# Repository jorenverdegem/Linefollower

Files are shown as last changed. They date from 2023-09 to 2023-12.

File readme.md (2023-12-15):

# LineFollower PLAN B:

400920108_895944135587999_7262908235151916565_n

# LineFollower PLAN A:

398428672_725404612801147_6601868790741897883_n

## specifications (Plan A)

microcontroller: ATmega32u4

motors: Mini Micro Metal Gear Motor 6V DC - Ratio 30:1

h-bridge: DRV8833 Dual Motor Driver Carrier

sensors: QTR-8A Reflectance Sensor Array

batteries: 18650 Li-ion batterijen

wireless communication: HC-05 Bluetooth module

distance sensor - motors: 70 mm

weight: 182 g

speed: 0.612 m/s

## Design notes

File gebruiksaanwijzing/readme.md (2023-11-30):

# Gebruiksaanwijzing

### opladen / vervangen batterijen
De batterijen kunnen van de wagen worden gehaald door de rekker rond de arduino los te maken. Indien de batterijen te stevig vast zitten kan men steeds een schroevendraaier gebruiken om ze los te krijgen.
Het is aangeraden steeds de spanning van deze batterijen te controleren met een multimeter. Als deze geen 8V meer leveren laad je ze best op. Dit kan door ze in liitokala oplader te steken, die is te vinden in de BOM.
Vanaf de lampjes groen zijn, hebben de batterijen weer voldoende spanning en kan de wagen zonder problemen even door rijden.

### draadloze communicatie
#### verbinding maken
Om verbinding te maken met de smartphone zorg je eerst dat de wagen voorzien is van de correcte spanning (de twee batterijen hebben samen >8V). 
Als tweede neem je de smarthpone en download je de app "Serial Bluetooth Terminal" (android). Deze app zal het mogelijk te communiceren met onze wagen.
Dit gebeurt aan de hand van verschillende commando's. De meest gebruikte commando's kunnen eenvoudig in 4 drukknoppen worden verwerkt. 
Deze 4 knoppen zijn op de foto in het geel aangeduid. Om deze net zoals mij te programmeren druk je lang op de knop en stel je de volgende zaken in:
Knop 1 -> Name: "on", Value: "run on"
Knop 2 -> Name: "off", Value: "run off"
Knop 3 -> Name: "debug", Value: "debug"
Knop 4 -> Name: "?", "cmd"

bewerkt403773356_2250373231799713_3687328011572819282_n

Om de connectie te maken ga je eerst naar de bluetoothinstelling van de telefoon en zoek je "HC-05". Vervolgens maak je verbinding en gebruik je de code "1234".
Eenmaal verbonden, kan je naar de app gaan en zou je deze bij "devices" moeten zien staan. Als laatste druk je op "connect" (de gele cirkel op bovenstaande foto). 
Als je de boodschap "connected" te zien krijgt, ben je volledig verbonden en klaar om commando's uit te sturen.

#### commando's
Er zijn verschillende commando's die gebruikt kunnen worden om parameters van de robot in te stellen, maar ook om zaken uit te lezen. De eerste 4 commando's zijn reeds verwerkt in de 4 drukknoppen en doen het volgende:
"on" -> stuurt commando "run on" -> Dit zal de motoren starten en de wagen doen rijden.
"off" -> stuurt commando "run off" -> Dit zal de motoren en de wagen doen stoppen.
"debug" -> stuurt commando "debug" -> Je krijgt een oplijsting van alle ingestelde parameters waarmee de wagen momenteel rijdt. 
"?" -> stuurt commando "cmd" -> Je krijgt een oplijsting van alle mogelijke commando's die buiten de knoppen ook kunnen worden ingegeven (zie foto).
405417769_639606544789889_332189492948155658_n

Volgende commando's kunnen dus ook nog worden ingegeven, en stellen een bepaalde parameter in:
set cycle [µs]  
set power [0..255]  
set diff [0..1]  
set kp [0..]  
set ki [0..]  
set kd [0..]

# vb. set ki 0.7 

Als laatste zijn er nog 2 andere commando's om de sensoren te calibreren. Dit wordt hieronder verder verduidelijkt.
calibrate black  
calibrate white  

### kalibratie
Wanneer er voor de eerste keer wordt gereden op een bepaald parkour is het belangrijk om de sensoren te calibreren. Dit zal er voor zorgen dat er een duidelijk verschil tussen wit en zwart wordt herkent.

# stap 1:
Plaats de wagen op een volledig wit stuk, en voer het commando "calibrate white" in. Wacht even tot je "done" ziet verschijnen.
# stap 2:
Plaats de wagen op een volledig zwart stuk, en voer het commando "calibrate black" in. Wacht even tot je "done" ziet verschijnen.

-> Nu zouden de sensoren een duidelijk verschil moeten uitlezen. Dit kan je controleren door "debug" in te voeren, en de "black" en "white" waardes te controleren. Deze moeten ver genoeg uit elkaar liggen om correct te kunnen werken.

### settings
De robot rijdt stabiel met volgende parameters:
405311322_893484695519741_7041870474847189614_n

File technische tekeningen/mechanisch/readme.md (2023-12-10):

Op deze pagina vind je het volgende terug:

- Mechanische tekening van de PCB.
- Mechanische tekening van de spoiler, die met de 3D printer kan worden afgeprint.

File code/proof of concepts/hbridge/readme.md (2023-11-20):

# H-Bridge proof of concept

Minimale hard- & software die aantoont dat 2 motoren onafhankelijk van elkaar kunnen draaien, en (traploos) regelbaar zijn in snelheid en draairichting.
Hiervoor wordt gebruik gemaakt van 2 "Mini Micro Metal Gear Motor 6V DC - Ratio 30:1" motoren en als H-brug gebruiken we de "DRV8833 Dual Motor Driver Carrier".

## Functionaliteit:

Het geschreven programma zal in een loop demonstreren hoe de motoren geleidelijk aan versnellen tot het maximale snelheid, en vervolgens weer vertragen naar 0. 
Vervolgens wordt gedemonstreerd dat ze ook in tegengestelde richting kunnen draaien, en ook afzonderlijk van elkaar een andere draairichting kunnen aannemen.

## Arduinocode:

image (11)
image (12)
image (13)

In de setup worden de pinnen die verbonden zijn met de H-brug als OUTPUT geconfigureerd en worden de motoren uitgezet.
Vervolgens begint te "void loop" functie waarin verschillende zaken gebeuren:
  1. De motoren gaan van stilstand geleidelijk aan naar hun maximale snelheid.
  2. De motoren blijven 2 seconden aan hun maximale snelheid draaien.
  3. De motoren vertragen van hun maximale snelheid naar stilstand.
  4. De motoren blijven 2 seconden uit.
  5. De maximale snelheid in tegengestelde draairichting worden op beide motoren gedemonstreerd voor 2 seconden.
  6. De motoren blijven 2 seconden uit.
  7. De motoren draaien 2 seconden aan hun maximale snelheid, maar beide met een andere draairichting.
  8. De motoren blijven 1 seconde uit.
  9. de motoren draaien 2 seconden aan hun maximale snelhied, maar nu beide in de andere richting dan de vorige stap.
  10. De motoren blijven 1 seconde uit

Vervolgens zijn nog 3 andere functies in gemaakt. Deze zullen ervoor zorgen dat we via de "spin_and_wait" functie overzichtelijk de snelheid kunnen geven aan de 2 motoren.
Ook wordt hier duidelijk gemaakt dat de draairichting moet veranderen als we een negatieve waarde ingeven en wordt de snelheid geschreven naar de seriële monitor.

## Elektronisch schema:

Het elektronisch schema voor deze schakeling ziet er als volgt uit:
Schema H-bruggen

## Testresultaten:

Op de seriële monitor kunnen we mooi volgen welke snelheid de motoren op dit moment hebben aangenomen:
image (14)

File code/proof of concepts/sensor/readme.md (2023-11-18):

# Sensoren proof of concept

minimale hard- en software die aantoont dat minimaal 6 sensoren onafhankelijk van elkaar kunnen uitgelezen worden (geen calibratie, normalisatie of interpolatie). Hierbij moet een zo groot mogelijk bereik van de AD converter benut worden (indien van toepassing).
Hiervoor wordt de QTR-8A gebruikt, waarbij de laatste 2 sensoren van de printplaat worden afgebroken.

## Arduino code:

De arduino code ziet er als volgt uit:

image (9)

Hierbij maken we gebruik van de QTRSensors.h library. Deze maakt het mogelijk om de sensor evenvoudig te configureren en de waardes uit te lezen.
Vervolgens worden deze 6 sensorwaardes naast elkaar geprint op de seriële monitor. Het resultaat ziet er als volgt uit:

image (10)

## Elektronisch schema:

Een elektronisch schema is bij deze schakeling overbodig, aangezien de 6 analoge outputs van de sensoren gewoon moeten verbonden worden met de 6 analoge inputs van de arduino.
Verder moet de sensor enkel nog gevoed worden met 5V, en moet ook de gnd worden verbonden.

QTR

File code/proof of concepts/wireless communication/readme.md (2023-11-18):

# draadloze communicatie proof of concept
Minimale hard- en software waarmee aangetoond wordt dat duplex kan gecommuniceerd worden tussen de microcontroller en een smartphone, gebruik makend van de HC-05 Bluetoothmodule.
Om de werking van de bluetoothmodule te demonstreren is een code geschreven waarbij we in 2 richtingen communiceren.

## Functionaliteit:
Als eerste zal de microcontroller een drukknop uitlezen en doorsturen naar de smartphone vanaf deze wordt ingedrukt.
Anderzijds kan de toestand van de "built-in led" op de microcontroller gewijzigd worden door 2 knoppen op de smartphone.
Als laatste is het ook mogelijk om tekstberichten van de smartphone naar de pc te sturen, en omgekeerd.

## Arduino code:
De arduino code ziet er als volgt uit:


Als eerste valt op dat we gebruik maken van de library "SoftwareSerial.h". Deze zorgt ervoor dat we een tweede softwarematige seriële monitor kunnen aanmaken, die wordt gebruikt door de smarthphone.
Als we kijken naar de eerste "if" structuur in de "void loop()" functie zien we dat de data wordt ingelezen van de seriële monitor van de smartphone, en wordt geschreven naar de seriële monitor van de computer.
Het omgekeerde gebeurd in de tweede "if" structuur. Op deze manier kunnen we al in twee richtingen berichten zenden.

In de derde "if" structuur wordt gezocht naar een '0' of een '1' in de data die binnenkomt vanaf de gsm. Dit is wat de knop op de gsm zal doorsturen als we de LED op de microcontroller willen laten branden.

Als laatste is ook een interruptfunctie toegevoegd met een debouncefunctie om de knop aan de microcontroller uit te lezen, en vervolgens een boodschap naar de gsm te sturen.
Dit principe kwam al eerder terug in de "Proof of concepts: interrupt".

## Elektronisch schema
Het elektronisch schema voor deze schakeling ziet er als volgt uit:

Merk op dat de RX van de bluetoothmodule niet rechtsreeks verbonden is met de TX van de microcontroller! Dit is belangrijk aangezien de HC-05 Bluetoothmodule met 3.3V signalen verwacht.
De arduino stuurt signalen van 5V. Daarom maken we een spanningsdeler met behulp van 2 weerstanden zodat we de 5V een stuk kunnen reduceren.

## Testresultaten
Op de smartphone ziet de seriële monitor er als volgt uit:
370057969_310741495226934_2358127417559545938_n
Onderaan zijn de knoppen "on" en "off" te zien. Deze werden ingedrukt en verstuurden een '1' en een '0'. De LED aan de microcontroller ging effectief aan en uit wanneer op de corresponderende knoppen werd gedrukt.
Vervolgens is op de knop aan de microcontroller gedrukt. Hier ontvingen we correct het bericht "De knop is ingedrukt!". Als laatste is via de seriële monitor van de computer nog een testbericht gestuurd naar de gsm.
Hierop is het antwoord "test van gsm naar pc" verstuurd. Dit zien we dan ook verschijnen op seriële monitor van de computer:


Als laatste is ook op de foto te zien dat de baudrate van onze seriële monitor is ingesteld op 9600 baud. Dit is belangrijk aangezien we dezelfde keuze hebben gemaakt in de arduinocode. Deze moeten overeenkomen!

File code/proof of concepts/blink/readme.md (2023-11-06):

# blink proof of concept
Om een led simpelweg te doen knipperen via een arduino, is de volgende code geschreven:



De built-in led in de arduino wordt geconfigureerd als output. Deze output wordt vervolgens herhaaldelijk om de seconde hoog gezet.
Wanneer we in de toekomst willen testen of de microcontroller nog steeds werkt naar behoren, kan dit programma simpelweg worden upgeload om zeker te zijn van ons zaak.

(Een schema wordt verder niet weergegeven, aangezien we de interne led van de arduino doen knipperen. Er wordt verder niks geschakeld aan de arduino.)

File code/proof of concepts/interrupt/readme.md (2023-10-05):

# start/stop interrupt proof of concept
Om de werking van een start/stop interrupt te demonstreren op een arduino, waarin softwarematig gezorgd is voor een debounce van de schakelaar, is de volgende code geschreven:

image (1)

De code werkt als volgt: als de schakelaar wordt ingedrukt waarmee men een start of stop signaal wilt genereren, zal via de "attachInterrupt" functie de loop hardwarematig onderbroken worden. Er hoeft dus niet telkens gepolled worden in de software om te kijken of de knop al dan niet is ingedrukt.
Als de intterupt wordt getriggerd wordt de functie "void interrupt()" uitgevoerd. Hierin wordt ter demonstratie de toestand van een led gewijzigd. Dit kan uiteraard vervangen worden door een start/stop signaal.

In deze interrupt zorgt de "millis()" functie er verder voor dat er geen debouncing kan optreden bij het indrukken van de schakelaar. De interrupt moet 100 ms actief zijn alvorens de functie effectief wordt uitgevoerd. Als ons knop dus even zou trillen, zal de functie geen meerdere keren worden uitgevoerd.

Vb: de knop trilt 3x met daartussen telkens 10 ms -> de functie zal maar 1x worden uitgevoerd aangezien de "if" functie zal zorgen voor een kleine delay.

Het elektronisch schema voor deze schakeling ziet er als volgt uit:



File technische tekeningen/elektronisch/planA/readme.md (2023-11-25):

## PCB ontwerp:



## PCB Top view:



## PCB Bottom view:



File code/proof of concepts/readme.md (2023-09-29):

# Proof of Concepts

Een proof of concept is een combinatie van minimale hard- en software om eenvoudig aan te tonen dat iets werkt.  
Proof of concepts kunnen enerzijds als eerste poging dienen om een bepaald onderdeel van het project werkend te krijgen. Anderzijds kunnen ze tijdens het debuggen van het finale project dienen als test om eventuele hardware problemen te elimineren bij onduidelijke problemen.
<br />  
<br />
Een proof of concept bestaat uit
* een elektronisch schema (indien van toepassing)
* minimale code om de voorop gestelde zaken te demonstreren
* minimale uitleg / aandachtspunten
<br />
De elektronische schakelingen van de proof of concepts komen bij voorkeur overeen met deze van de uiteindelijke linefollower, zodat de code zonder aanpassingen op het finale project kan draaien.

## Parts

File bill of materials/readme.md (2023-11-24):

## bill of materials
<br />

|volgnummer |naam |omschrijving |nieuw/recup |kostprijs/stuk |aantal  |subtotaal |
|--- |---- |--- |--- |--- |---  |--- |
|1 |Microcontroller |ATmega32u4 (Arduino Leonardo) |Recup |€12,99 |1 |€12,99 |
|2 |Mini Micro Metal Gear Motor 30:1 |6V DC Gear Motor |Nieuw |€3,56 |2 |€7,12 |
|3 |H-brug |DRV8833 Dual Motor Driver Carrier |Nieuw |€12,52 |1 |€12,52 |
|4 |Infrared Reflection Sensors (8) |QTR-8A Reflectance Sensor Array |Nieuw |€16,13 |1 |€16,13 |
|5 |18650 Li-ion Batterijen |Rechargeable Battery (3,7V - 19800mAh)|Nieuw |€2,63 |2 |€5,26 |
|6 |Batterijhouder |18650 Dubbele batterijhouder |Nieuw |€2,39 |1 |€2,39 |
|7 |Batterijoplader |LiitoKala Lii-L2 3,7V 18650 |Nieuw |€10,17 |1 |€10,17 |
|8 |Bluetooth Module |HC-05 |Recup |€11,96 |1 |€11,96 |
|9 |Wielhouders |Micro Metal Gearmotor Bracket Pair |Nieuw |€5,39 |1 |€5,39 |
|10 |Wielen |Polulu wheel 40x7mm Pair - Red |Nieuw |€7,69 |1 |€7,69 |
|11 |Weerstanden |1x1kOhm en 1x2kOhm OF 3x1kOhm |Recup |/ |3 |/ |
|12 |Dupont-draadjes |20xman-vrouw en 5xman-man |Recup |/ |25 |/ |

### Totale kostprijs: €91,62

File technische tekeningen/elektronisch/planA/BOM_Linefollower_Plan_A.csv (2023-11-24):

ID | Name | Designator | Footprint | Quantity | Manufacturer Part | Manufacturer | Supplier | Supplier Part | Price
1 | 18650x2 | H1 | H18650 | 1
2 | ARDUINO_LEONARDO | U1 | ARDUINO_LEONARDO | 1
3 | DRV8833 | U2 | DRV8833 DUAL MOTOR DRIVER CARRIER | 1
4 | HC05 | U3 | HC-05 | 1 | HC05
5 | QTR8A | U4 | QTR8A | 1 | QTR8A | POLOLU | POLOLU
6 | Micro metal gearmotor | U5,U6 | MICRO METAL GEAR MOTOR | 2 | 3062 | Pololu | Pololu | 3062

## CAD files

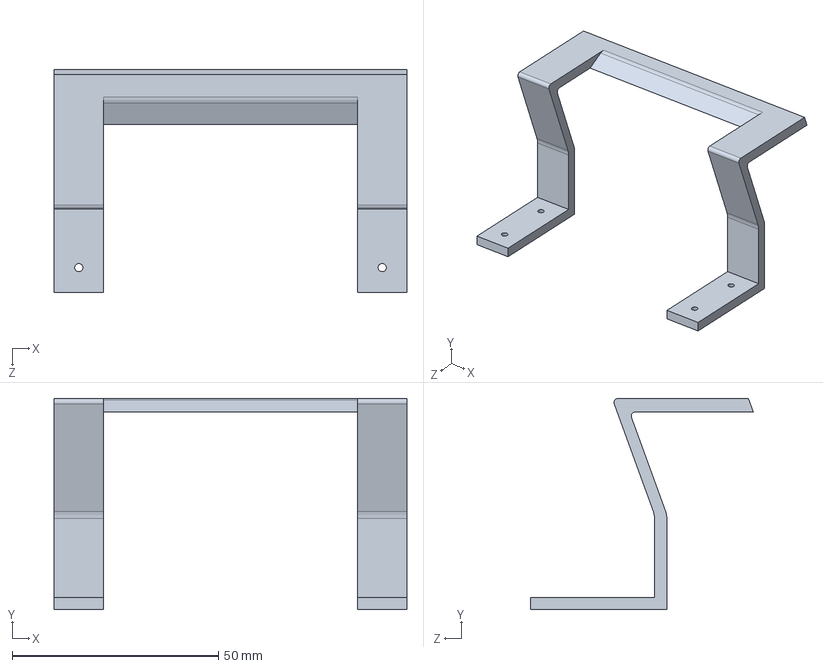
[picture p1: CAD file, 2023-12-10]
technische tekeningen/mechanisch/spoiler.SLDPRT
85.5 x 51.2 x 53.9 mm

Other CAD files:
technische tekeningen/mechanisch/Spoiler.STL

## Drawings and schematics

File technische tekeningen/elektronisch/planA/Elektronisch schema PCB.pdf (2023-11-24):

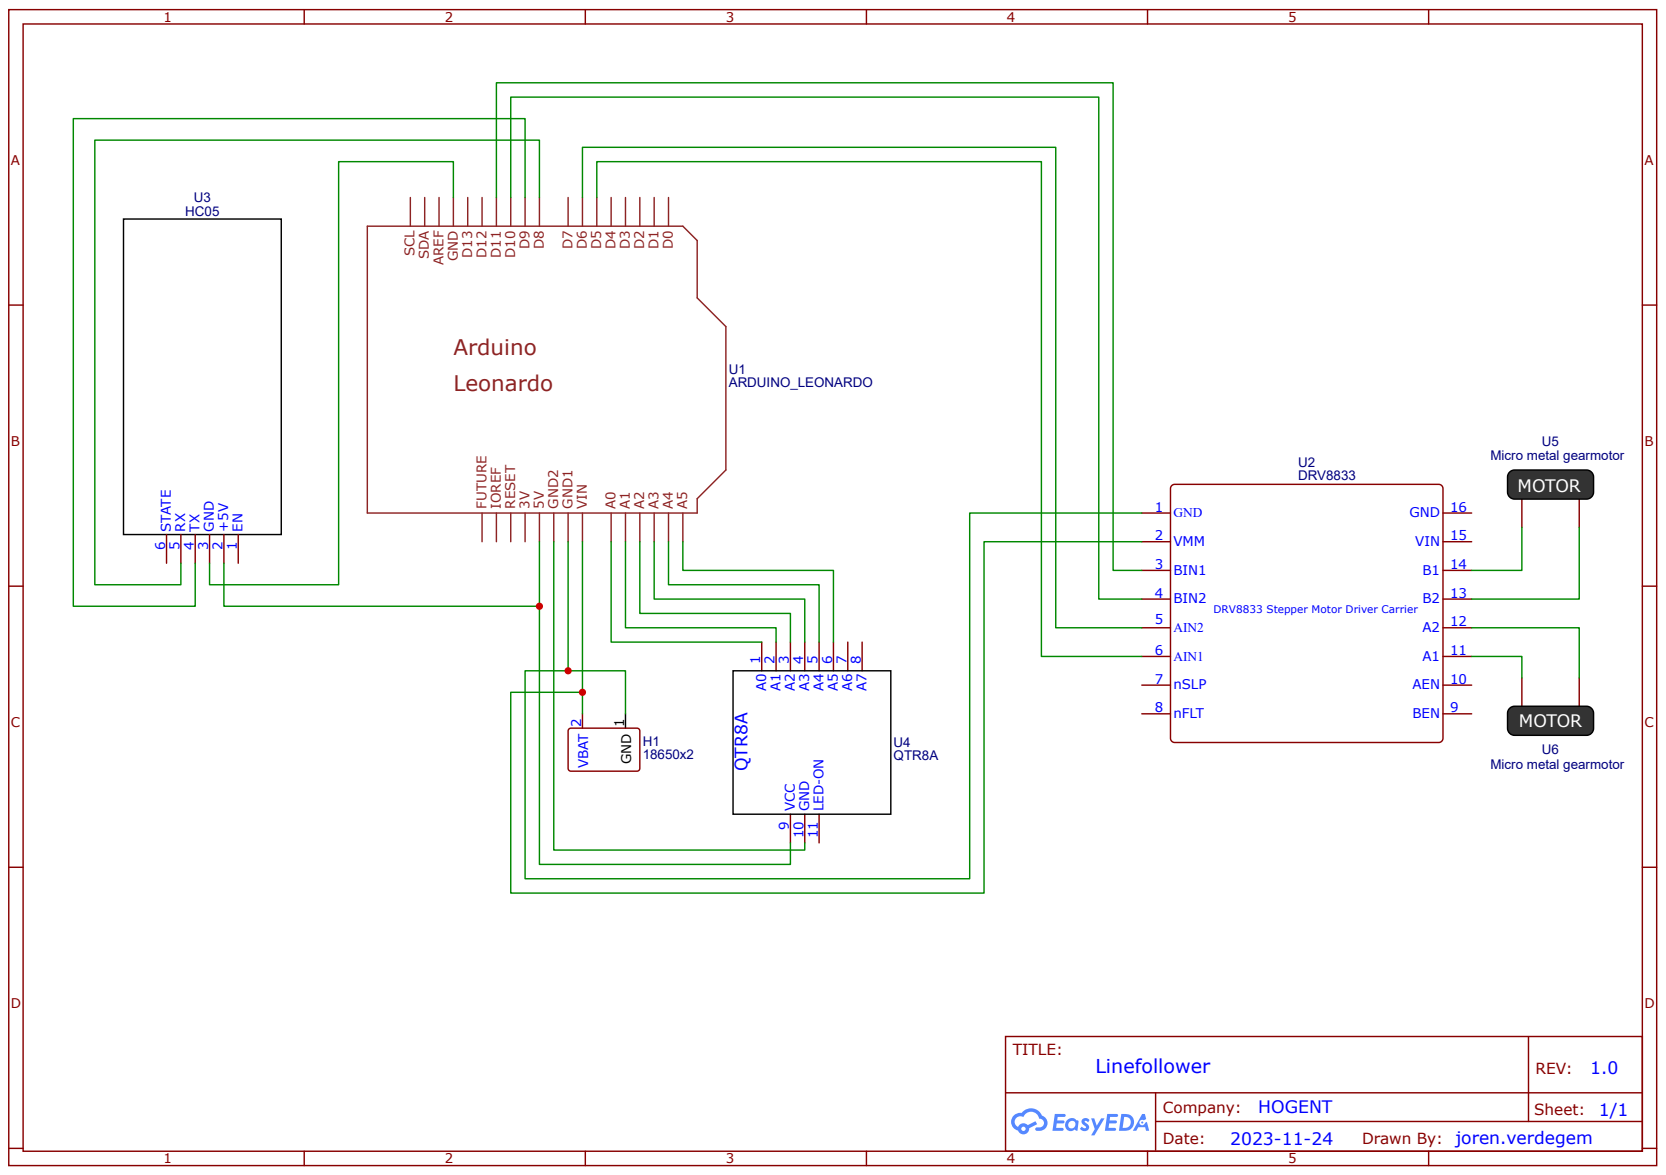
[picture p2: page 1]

DRV8833 Stepper Motor Driver Carrier

Drawn By: joren.verdegem

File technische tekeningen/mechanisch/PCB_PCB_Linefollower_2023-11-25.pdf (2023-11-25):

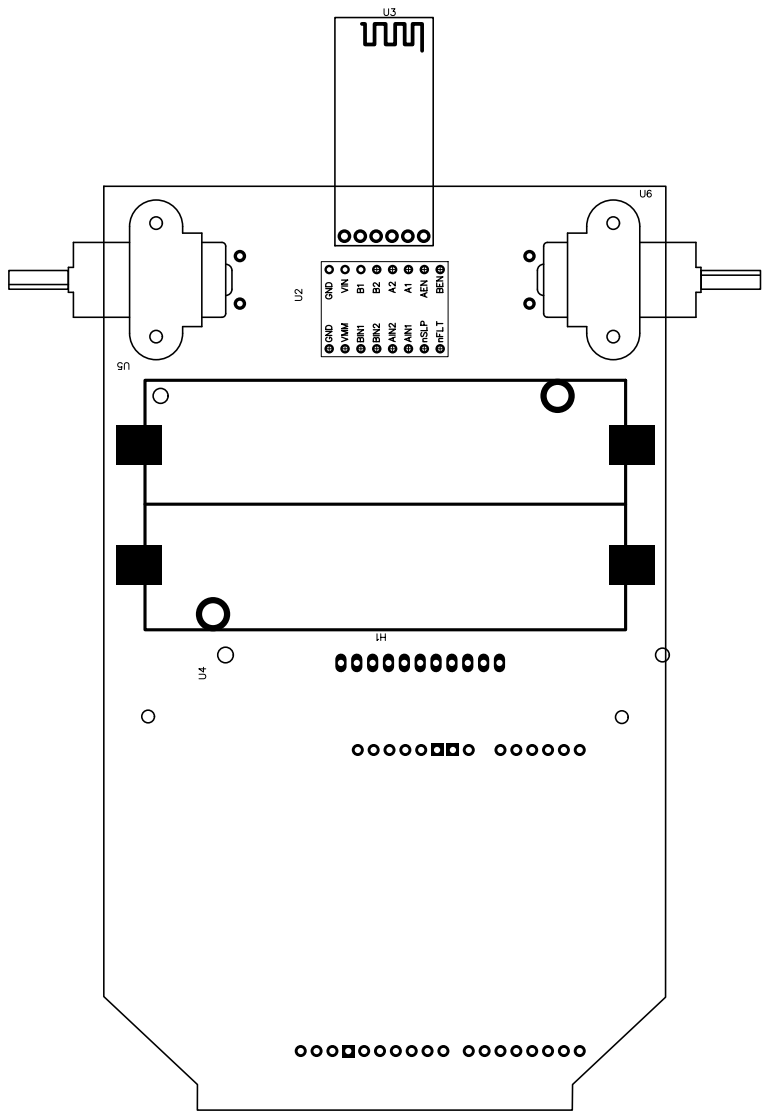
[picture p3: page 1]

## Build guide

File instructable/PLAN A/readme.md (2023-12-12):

# Instructable

Nadat we Plan B hebben samengesteld, kiezen we ervoor om het resultaat nog mooier afwerken. Het idee is om een printplaat te ontwerpen, die kan dienen als frame voor onze wagen. Hierbij zullen dus geen dupon meer nodig zijn, wat zal zorgen voor een mooier afgewerkt geheel. Op de printplaat zorgen we dus voor alle connecties tussen de verschillende componenten, met bijhorende gaten zodat we onze componenten hierop kunnen solderen.

### stap 1

<br />

|volgnummer |naam |omschrijving |nieuw/recup |kostprijs/stuk |aantal  |subtotaal |
|--- |---- |--- |--- |--- |---  |--- |
|1 |Microcontroller |ATmega32u4 (Arduino Leonardo) |Recup |€12,99 |1 |€12,99 |
|2 |Mini Micro Metal Gear Motor 30:1 |6V DC Gear Motor |Nieuw |€3,56 |2 |€7,12 |
|3 |H-brug |DRV8833 Dual Motor Driver Carrier |Nieuw |€12,52 |1 |€12,52 |
|4 |Infrared Reflection Sensors (8) |QTR-8A Reflectance Sensor Array |Nieuw |€16,13 |1 |€16,13 |
|5 |18650 Li-ion Batterijen |Rechargeable Battery (3,7V - 19800mAh)|Nieuw |€2,63 |2 |€5,26 |
|6 |Batterijhouder |18650 Dubbele batterijhouder |Nieuw |€2,39 |1 |€2,39 |
|7 |Batterijoplader |LiitoKala Lii-L2 3,7V 18650 |Nieuw |€10,17 |1 |€10,17 |
|8 |Bluetooth Module |HC-05 |Recup |€11,96 |1 |€11,96 |
|9 |Wielhouders |Micro Metal Gearmotor Bracket Pair |Nieuw |€5,39 |1 |€5,39 |
|10 |Wielen |Polulu wheel 40x7mm Pair - Red |Nieuw |€7,69 |1 |€7,69 |
|11 |Pinheaders | |Recup |/ |40 |/ |

Nu we alle componenten hebben, kunnen we de printplaat beginnen ontwerpen. Dit werd gedaan via de website: https://easyeda.com/editor .
Het ontwerpen van deze printplaat gebeurd in 3 stappen.

### stap 2

Je tekent een elektronisch schema, waarbij je alle componenten terugzoekt in het programma. Het is belangrijk dat je de exacte componenten invoegt, zodat de afmetingen in de latere fases overeenkomen met onze componenten. Het elektrisch schema dat ik heb ontworpen is terug te vinden via de volgende link: https://github.com/jorenverdegem/Linefollower/tree/main/technische%20tekeningen/elektronisch/planA . Hierbij kan de JSON worden gebruikt om rechtsreeks in het programma te voegen, dan hoef je het schema niet meer zelf te tekenen.

## !BELANGRIJK! 
De component "DRV8833" staat verkeerd getekend in dit programma. De gaatjes voor de pinnen zijn te klein, en de component is 5 mm te dik getekend. Je gaat hier dus best opzoek naar de juiste component, of past de tekening aan zodat ze overeen komt met de afmetingen uit de datasheet.
Let er verder ook op dat je de QTR-8A sensor niet perfect in het midden plaatst! Wij maken enkel gebruik van de eerste 6 sensoren (want een arduino heeft maar 6 analoge inputs), waardoor het midden van de sensor zich op een andere positie bevindt. Zorg dat dit overeenkomt!

### stap 3

Nadat je het elektronisch schema hebt gemaakt, en gecontroleerd hebt dat alles correct is aangesloten kan je beginnen aan het mechanisch ontwerp. Hierbij kies je waar welke component staat op de printplaat, en kan je ook de vorm aanpassen. Mijn mechanische tekening is terug te vinden via de volgende link: https://github.com/jorenverdegem/Linefollower/blob/main/technische%20tekeningen/elektronisch/planA/readme.md .

### stap 4

Als laatste ga je op de mechanische tekening de verbindingen tekenen. Je kan dit automatisch laten genereren, maar ik raad aan om handmatig de verbindingen te leggen. Zo controleer je zelf nog eens of alles goed zit aangesloten. Mijn uiteindelijke PCB ontwerp is te vinden via de volgende link: https://github.com/jorenverdegem/Linefollower/tree/main/technische%20tekeningen/elektronisch/planA .

### stap 5

Nu alles is getekend kan je de pcb bestellen en hem laten maken. Dit alles duurt tussen de 1 à 2 weken.

#### Resultaat:

403398636_370587428807641_8804265821271583842_n

386886413_1037275554153914_3952061519202620705_n

### stap 6

Als de printplaat is toegekomen kan je starten met het solderen van je componenten.
- Waar de arduino komt, soldeer je pinheaders. Op deze manier kan je de arduino er steeds opklikken en weer afhalen.
- De QTR-8A sensor soldeer je aan de onderkant van de printplaat, zodat de sensoren naar de grond kijken.
- De batterijhouder kan je vastkleven met stevige lijm tegen de printplaat. De 2 draadjes soldeer je vast op de voorziene metalen vierkantjes.
- De bluetoothmodule kan je rechtopstaand solderen. Zorg ervoor dat de pinnen (zoals vcc en gnd) overeenkomen met de juiste gaatjes op de pcb.
- De motoren maak je vast met de bijhorende beugels, de gaatjes zijn hiervoor perfect gepositioneerd.
- De H-brug soldeer je ook vast op de correcte plek

Als alles goed vast zit kan je het geheel opnieuw beginnen testen. Indien er iets misloopt is het interessant om de proof of concepts er weer bij te halen en alles terug afzonderlijk te testen.
Zo was bij mij het geval dat een van de motoren kapot was gegaan. Deze werd zeer warm en draaide niet meer bij zeer lage snelheden. Ook als de reductie ervan tussen werd gehaald deden dezelfde problemen zich voor.

Indien je net zoals mij de fout hebt gemaakt om de component "DRV8833" zonder aanpassen in het pcb programma te gebruiken, kan je de component toch nog solderen aan de hand van vrouwelijke pinheaders, die wat schuin worden geplaatst. Het resultaat oogt iets minder mooi, maar ziet er als volgt uit:

377144747_2392994354217988_3845947637720984982_n

### stap 7

Proficiat! Nu alles werkt heb je een werkend geheel! Nu de wagen tot leven is gekomen kan je gaan spelen met de verschillende parameters, tot je het snelheidsrecord breekt!
Om het geheel helemaal af te werken kan je er eventueel ook een spoiler op monteren. Een getekende spoiler die kan worden afgedrukt met een 3D printer is te vinden via de volgende link:
https://github.com/jorenverdegem/Linefollower/tree/main/technische%20tekeningen/mechanisch 
Deze kan worden gemonteerd aan de onderkant van de pcb, met dezelfde vijsjes als waarmee de motoren zijn gemonteerd.

### eindresultaat:

398428672_725404612801147_6601868790741897883_n

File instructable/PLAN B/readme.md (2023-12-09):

# Instructable

Vooraleer we aan ons plan A beginnen, testen we eerst ons programma en de wagen zonder een printplaat te bestellen. In deze instructable wordt stap voor stap beschreven hoe we alle componenten samenstellen, met een werkende wagen als resultaat.

### stap 1
Bestel alle componenten uit de bill of materials: 
<br />

|volgnummer |naam |omschrijving |nieuw/recup |kostprijs/stuk |aantal  |subtotaal |
|--- |---- |--- |--- |--- |---  |--- |
|1 |Microcontroller |ATmega32u4 (Arduino Leonardo) |Recup |€12,99 |1 |€12,99 |
|2 |Mini Micro Metal Gear Motor 30:1 |6V DC Gear Motor |Nieuw |€3,56 |2 |€7,12 |
|3 |H-brug |DRV8833 Dual Motor Driver Carrier |Nieuw |€12,52 |1 |€12,52 |
|4 |Infrared Reflection Sensors (8) |QTR-8A Reflectance Sensor Array |Nieuw |€16,13 |1 |€16,13 |
|5 |18650 Li-ion Batterijen |Rechargeable Battery (3,7V - 19800mAh)|Nieuw |€2,63 |2 |€5,26 |
|6 |Batterijhouder |18650 Dubbele batterijhouder |Nieuw |€2,39 |1 |€2,39 |
|7 |Batterijoplader |LiitoKala Lii-L2 3,7V 18650 |Nieuw |€10,17 |1 |€10,17 |
|8 |Bluetooth Module |HC-05 |Recup |€11,96 |1 |€11,96 |
|9 |Wielhouders |Micro Metal Gearmotor Bracket Pair |Nieuw |€5,39 |1 |€5,39 |
|10 |Wielen |Polulu wheel 40x7mm Pair - Red |Nieuw |€7,69 |1 |€7,69 |
|11 |Dupont-draadjes |20xman-vrouw en 5xman-man |Recup |/ |25 |/ |

Verder zijn er nog een aantal andere benodigdheden, zoals houten blokjes, een houten plank en extra wielen, maar deze zijn optioneel en kunnen perfect vervangen worden door andere recup-materialen.

### stap 2
Nu we al het materiaal beschikbaar hebben, stellen we de linefollower samen. Als frame van de auto ga je best opzoek naar een houten plankje, of ander recupmateriaal die ongeveer een afmeting hebben van 160x100mm.
Er kan voor gekozen worden om met een figuurzaag extra vorm te geven, zodat dit het frame van een gestroomlijnde wagen kan voorstellen. Dit kan uiteraard ook achteraf gebeuren.
403679670_808460354413685_5912383544201351500_n
Vervolgens monteren we de batterijhouder op ons houten frame. Deze zetten we op de achterkant van onze plank, mooi in het midden. Ernaast worden 2 blokjes (500x250x10mm) geplakt, zodat we later de arduino boven de batterijhouder kunnen plaatsen. Het vastplakken van de houtblokjes en batterijhouder kan gebeuren met behulp van houtlijm.
405333687_223592240758807_7123575042251916946_n

### stap 3
In deze stap gaan we de motoren monteren op het frame. Hiervoor gebruiken we de "wielhouders" die samen met de motoren werden aangekocht. Bij het monteren van deze houders is het belangrijk dat ze allebei op de zelfde afstand worden gemonteerd, zodat ze mooi in lijn liggen met elkaar en de auto dus niet scheef zal gaan rijden. Via de volgende 2 foto's kan worden afgeleid waar ik deze ongeveer heb gemonteerd:

405266047_1487613928690795_4685521728919634876_n
404350260_309790145228844_7951685887738030043_n

Vervolgens werden gaatjes geboord, zodat de bijgeleverde boutjes gemakkelijk in het hout konden worden gedraaid.

405154670_3388969721320824_5026883236161777480_n
405283208_1006741277289677_2358455657544103621_n

Als laatste solderen we 2 dupontdraadjes aan de motoren, alvorens we deze vaststeken in de gemonteerde klemmen. Dit zodat we alle ruimte hebben om dit te kunnen doen.

403688872_365273492548581_5732422698806328131_n

### stap 4
Om de andere componenten, zoals de H-Brug en de bluetooth module te monteren gebruiken we simpelweg een elastiekje zodat alles mooi blijft zitten.

405139945_312554088254143_3331511207421659937_n

Vervolgens nemen we het elektronisch schema erbij en gaan we alles aansluiten aan de hand van dupont-draadjes. In het schema is te zien dat er 3 knooppunten zijn. 2 bij de batterijspanning en 1 bij de 5V spanning. Hiervoor gaan we gebruik maken van 3 kroonklemmen:

403625895_3664321383829692_851847983461746198_n 

Ook de sensor moet nog worden gemonteerd aan de onderzijde van de wagen. Hiervoor werden als eerst de twee sensoren die afzonderlijk kunnen werken van het breakout board gebroken. Zo hebben we nog steeds 6 sensoren, wat alles wat compacter maakt.


Hierna meten we af waar de draadjes via de onderkant van ons frame naarboven zullen komen, als de sensor mooi in het midden gemonteerd zit. Op deze plek worden verschillende gaatjes geboord, waar we uiteindelijk een mooie gleuf van maken:

403804083_266288663098954_5267448171383346415_n 

405217240_2342251582633342_3867722100881489745_n

Als laatste word de sensor nog eens extra vastgezet door 2 kleine boutjes in het frame te vijzen.

403641477_1091571545612815_5156694672164627113_n

### stap 5
In de voorlaatste stap zetten we de arduino op de twee houten blokjes, die we opnieuw vastmaken met een simpel elastiekje. Vervolgens verbinden we alle componenten, zoals in het elektronisch schema wordt weergegeven:



(In dit schema worden nog 2 weerstanden gebruikt om de spanning voor de bluetooth module te beperken. Na wat onderzoek op het internet bleek dit niet nodig te zijn, dus mag deze rechtsreeks verbonden worden met de pin op de arduino.)

405132827_636497835104419_2663353506568405863_n

De 3 kroonklemmen kunnen opnieuw met houtlijm worden vastgeplakt op de voorzijde van het frame. Als extra optie kunnen ook twee extra wielen worden gemonteerd aan de voorzijde. Je kan er ook voor kiezen om de auto te laten slepen.

403647766_1569203267187191_374478284157019129_n

Indien de voorgaande stappen correct werden gevolgd, zou het eindresultaat er ongeveer zo moeten uitzien:

400920108_895944135587999_7262908235151916565_n

### stap 6
Nu moeten we enkel nog het juiste programma gaan uploaden in de arduino. De code die moeten worden upgeload kan worden teruggevonden als bestand in deze repository. Als je dit bestand opent met de arduino IDE software kan linksboven op de upload knop worden gedrukt. Nadat het uploaden is geslaagd kunnen de batterijen in de auto worden gestopt, kan verbinding via bluetooth worden gemaakt met de telefoon, en zal de auto werken!
(Voor meer info over de bediening van de auto via bluetooth, zie https://github.com/jorenverdegem/Linefollower/tree/main/gebruiksaanwijzing .

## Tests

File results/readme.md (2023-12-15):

## resultaten plan B:

https://github.com/jorenverdegem/Linefollower/assets/146443076/7db539b1-5014-4cc6-ba4d-676c41c67225

## resultaten plan A:

https://github.com/jorenverdegem/Linefollower/assets/146443076/3100eb84-6c1c-4927-8e89-c5956f6eee93

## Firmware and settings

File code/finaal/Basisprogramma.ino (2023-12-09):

 #include "Arduino.h"
#include "SerialCommand.h"
#include "EEPROMAnything.h"
#include <SoftwareSerial.h>
 
const byte rxPin = 9;
const byte txPin = 8;
#define Baudrate 9600

#define MotorLeftForward 10
#define MotorLeftBackward 11
#define MotorRightForward 5
#define MotorRightBackward 6

SoftwareSerial BTSerial(rxPin, txPin); // RX TX
SerialCommand sCmd(BTSerial);
bool debug;
bool run;
unsigned long previous, calculationTime;

const int sensor[] = {A0, A1, A2, A3, A4, A5};
struct param_t
{
  unsigned long cycleTime;
  int black[6];
  int white[6];
  int power;
  float diff;
  float kp;
  float ki;
  float kd;
  //andere parameters die in het geheugen moeten
} params;

int normalised[6];
float debugPosition;
float iTerm, lastErr;

void setup()
{
  pinMode(rxPin, INPUT);
  pinMode(txPin, OUTPUT);
  BTSerial.begin(Baudrate);
  sCmd.addCommand("set", onSet);
  sCmd.addCommand("debug", onDebug);
  sCmd.addCommand("calibrate", onCalibrate);
  sCmd.addCommand("run", onRun);
  sCmd.addCommand("cmd", onCmd);
  sCmd.setDefaultHandler(onUnknownCommand);

  EEPROM_readAnything(0, params);
  
  BTSerial.println("ready");
}

void loop()
{
 sCmd.readSerial();

 unsigned long current = micros();
 if (current - previous >= params.cycleTime)
 {
  previous = current;
  
  //Waardes normaliseren: 
  for (int i = 0; i < 6; i++) normalised[i] = map(analogRead(sensor[i]), params.black[i], params.white[i], 0, 1000);

  //Kwadratische interpolatie:
  int index = 0;
  float position;
  for (int i=1; i < 6; i++) if (normalised[i] < normalised[index]) index = i;

  if (index == 0) position = -20;
  else if (index == 5) position = 20;
  else
  {
    int sNul = normalised[index];
    int sMinEen = normalised[index-1];
    int sPlusEen = normalised[index+1];

    float b = sPlusEen - sMinEen;
    b = b / 2;
    float a = sPlusEen - b - sNul;
    position = -b /(2 * a);
    position += index;
    position -= 2.5;
    position *= 10;
  }
  debugPosition = position;

  //PID
  float error = -position;
  float output = error * params.kp;
  iTerm += params.ki * error;
  iTerm = constrain(iTerm, -510, 510);
  output += iTerm;
  output += params.kd * (error - lastErr);
  lastErr = error;
  output = constrain(output, -510, 510);
  
  int powerLeft = 0;
  int powerRight = 0;

  if (run) if (output >= 0)
  {
    powerLeft = constrain(params.power + params.diff * output, -255, 255);
    powerRight = constrain(powerLeft - output, -255, 255);
    powerLeft = powerRight + output;
  }
  else
  {
    powerRight = constrain(params.power - params.diff * output, -255, 255);
    powerLeft = constrain(powerRight + output, -255, 255);
    powerRight = powerLeft - output;
  }
  
  analogWrite(MotorLeftForward, powerLeft > 0 ? powerLeft : 0);
  analogWrite(MotorLeftBackward, powerLeft < 0 ? -powerLeft : 0);
  analogWrite(MotorRightForward, powerRight > 0 ? powerRight : 0);
  analogWrite(MotorRightBackward, powerRight < 0 ? -powerRight : 0);
  
 }
 unsigned long difference = micros() - current;
 if (difference > calculationTime) calculationTime = difference;
}

void onSet()
{
  char* parameter = sCmd.next();
  char* value = sCmd.next();

  if (strcmp(parameter, "cycle") == 0)
  {
    long newCycleTime = atol(value);
    float ratio = ((float) newCycleTime) / ((float) params.cycleTime);
    params.ki *= ratio;
    params.kd /= ratio;
    params.cycleTime = newCycleTime;
  }
  else if (strcmp(parameter, "power") == 0) params.power = atol(value);
  else if (strcmp(parameter, "diff") == 0) params.diff = atof(value);
  else if (strcmp(parameter, "kp") == 0) params.kp = atof(value);
  else if (strcmp(parameter, "ki") ==0)
  {
    float cycleTimeInSec = ((float) params.cycleTime) / 1000000;
    params.ki = atof(value) * cycleTimeInSec;
  }
  else if (strcmp(parameter, "kd") ==0)
  {
    float cycleTimeInSec = ((float) params.cycleTime) / 1000000;
    params.kd = atof(value) / cycleTimeInSec;
  }
  else BTSerial.println("unknown paramameter");

  EEPROM_writeAnything(0, params);
}

void onDebug()
{
  BTSerial.print("cycle time: ");
  BTSerial.println(params.cycleTime);

  BTSerial.print("black: ");
  for (int i = 0; i < 6; i++)
  {
    BTSerial.print(params.black[i]);
    BTSerial.print(" ");    
  }
  BTSerial.println(" ");
  
  BTSerial.print("white: ");
  for (int i = 0; i < 6; i++)
  {
    BTSerial.print(params.white[i]);
    BTSerial.print(" ");    
  }
  BTSerial.println(" "); 

  BTSerial.print("normalised: ");
  for (int i = 0; i < 6; i++)
  {
    BTSerial.print(normalised[i]);
    BTSerial.print(" ");    
  }
  BTSerial.println(" ");

  BTSerial.print("position: ");
  BTSerial.println(debugPosition);

  BTSerial.print("power: ");
  BTSerial.println(params.power);

  BTSerial.print("diff: ");
  BTSerial.println(params.diff);

  BTSerial.print("Kp: ");
  BTSerial.println(params.kp);

  float cycleTimeInSec = ((float) params.cycleTime) / 1000000;
  float ki = params.ki / cycleTimeInSec;
  BTSerial.print("Ki: ");
  BTSerial.println(ki);
  
  float kd = params.kd * cycleTimeInSec;
  BTSerial.print("Kd: ");
  BTSerial.println(kd);

  BTSerial.print("calculation time: ");
  BTSerial.println(calculationTime);
  calculationTime = 0;
}

void onCalibrate()
{
  char* parameter = sCmd.next();
  if (strcmp(parameter, "black") == 0)
  {
    BTSerial.print("start calibrating black... ");
    for (int i = 0; i < 6; i++) params.black[i] = analogRead(sensor[i]);
    BTSerial.print("done");
  }
  else if (strcmp(parameter, "white") == 0)
  {
    BTSerial.print("start calibrating white... ");
    for (int i = 0; i < 6; i++) params.white[i] = analogRead(sensor[i]);
    BTSerial.print("done");
  }
  EEPROM_writeAnything(0, params);
}

void onRun()
{
  char* parameter = sCmd.next();
  char* value = sCmd.next();

  if (strcmp(parameter, "on") == 0)
  {
   iTerm = 0;
   run = true;
  }
  else run = false;
}

void onCmd()
{
  BTSerial.println("-------Possible commands:-------");
  BTSerial.println("calibrate white");
  BTSerial.println("calibrate black");
  BTSerial.println("set cycle 'x' (<10000 µs");
  BTSerial.println("set power 'x' (0...255)");
  BTSerial.println("set diff 'x' (0...1)");
  BTSerial.println("set kp 'x'");
  BTSerial.println("set ki 'x'");
  BTSerial.println("set kd 'x'");
}

void onUnknownCommand(char* command)
{
  BTSerial.print("Unknown Command: \"");
  BTSerial.print(command);
  BTSerial.println("\"");
}
